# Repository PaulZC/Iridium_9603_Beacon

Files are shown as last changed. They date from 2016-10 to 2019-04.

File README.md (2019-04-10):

# Iridium 9603N Beacon

A lightweight Iridium 9603N + GNSS Beacon (Tracker)

Suitable for high altitude ballooning, asset tracking and many other remote monitoring applications.

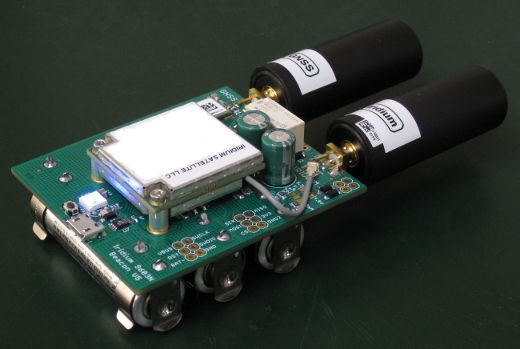
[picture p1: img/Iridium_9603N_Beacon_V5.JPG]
Iridium_9603N_Beacon_V5


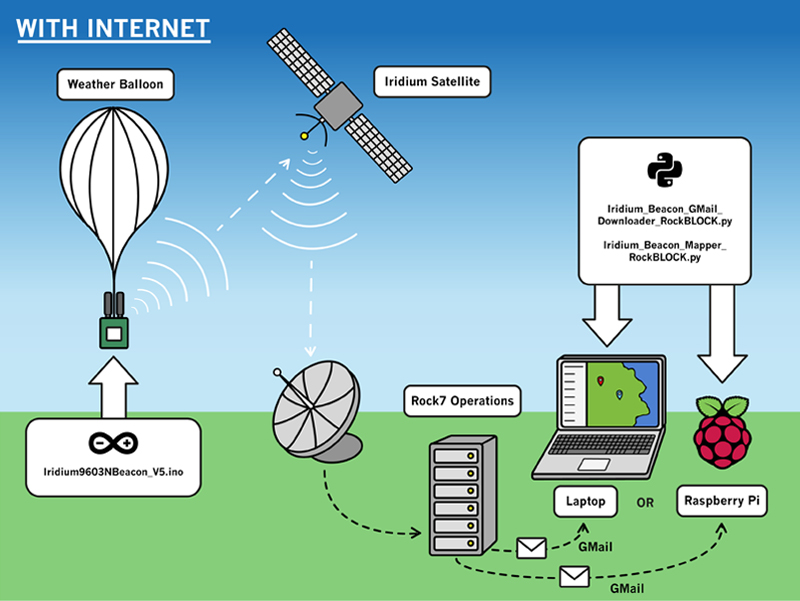
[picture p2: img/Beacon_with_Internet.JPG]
Beacon with Internet


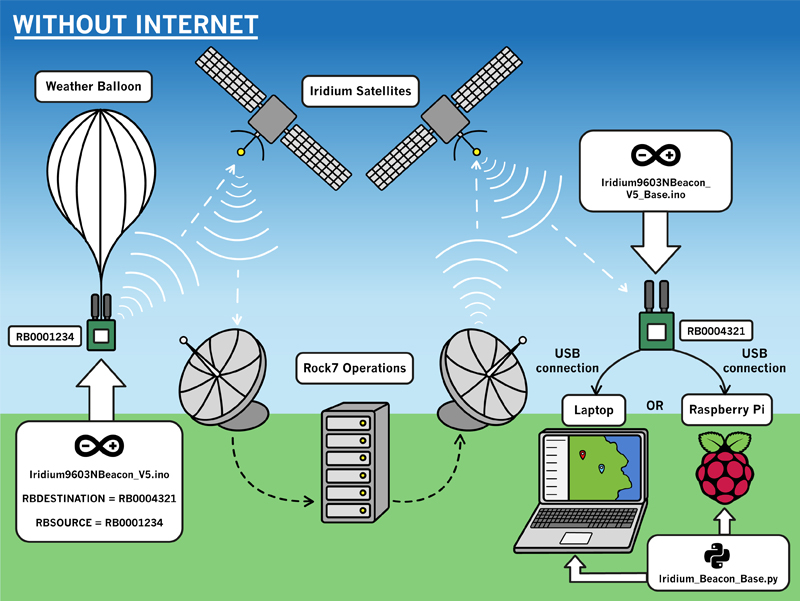
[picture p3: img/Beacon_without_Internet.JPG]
Beacon without Internet


**See [LEARN.md](https://github.com/PaulZC/Iridium_9603_Beacon/blob/master/LEARN.md) for more details.**

**See [ASSEMBLY.md](https://github.com/PaulZC/Iridium_9603_Beacon/blob/master/ASSEMBLY.md) for details on how to assemble the PCB.**

**See [RockBLOCK.md](https://github.com/PaulZC/Iridium_9603_Beacon/blob/master/RockBLOCK.md) for details on how to track your beacon from _anywhere_ using Rock7 RockBLOCK Gateway messaging.**

See [Iridium_9603_Beacon_V5.pdf](https://github.com/PaulZC/Iridium_9603_Beacon/blob/master/Iridium_9603_Beacon_V5.pdf) for the schematic, layout and Bill Of Materials.

See [Iridium_9603_Beacon_V5_BOM.xls](https://github.com/PaulZC/Iridium_9603_Beacon/blob/master/Iridium_9603_Beacon_V5_BOM.xls) for the Bill Of Materials in Excel format.

The [Eagle](https://github.com/PaulZC/Iridium_9603_Beacon/tree/master/Eagle) directory contains the schematic and pcb design files.

The [Gerber](https://github.com/PaulZC/Iridium_9603_Beacon/tree/master/Gerber) directory contains the Gerber files for the PCB. These files have been checked and used to manufacture a batch of circuit boards.

The [Arduino](https://github.com/PaulZC/Iridium_9603_Beacon/tree/master/Arduino) directory contains the Arduino code.

The [OpenSCAD](https://github.com/PaulZC/Iridium_9603_Beacon/tree/master/OpenSCAD) directory contains the .stl and .scad files for the 3D-printed covers.

The [Python](https://github.com/PaulZC/Iridium_9603_Beacon/tree/master/Python) directory contains tracking/mapping software based on the Google Static Maps API.

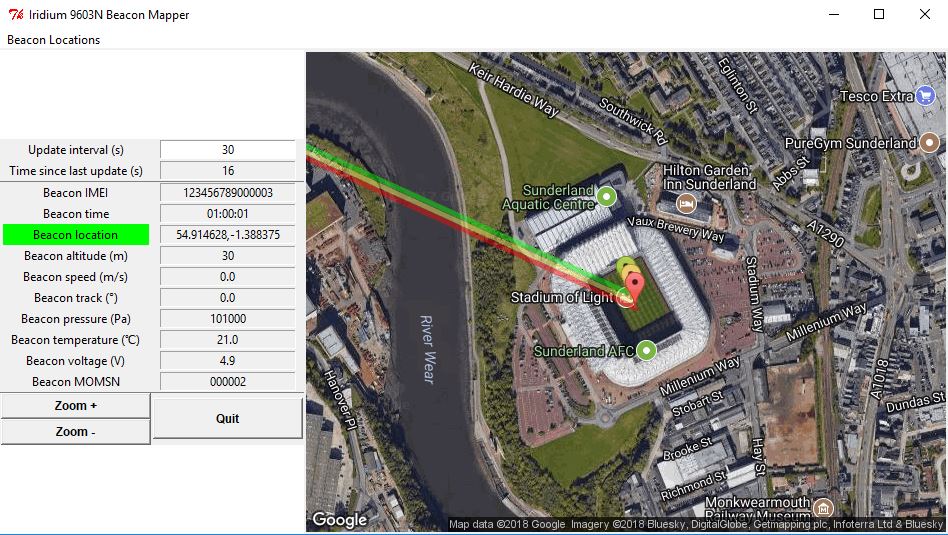
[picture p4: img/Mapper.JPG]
Mapper


See [Iridium Beacon Radio Board](https://github.com/PaulZC/Iridium_Beacon_Radio_Board) for details of the optional radio board.

Vector graphics by [Alice Clark](https://www.alicelclark.co.uk/about)

If you have found this project useful and if you are able to, please cite the paper:

P. Clark et al, An open source toolkit for the tracking, termination and recovery of high altitude balloon flights and payloads, 2019 JINST 14 P04003
[DOI:10.1088/1748-0221/14/04/P04003](https://doi.org/10.1088/1748-0221/14/04/P04003)

The Accepted Manuscript is available on arXiv: http://arxiv.org/abs/1904.04321

This project is distributed under a Creative Commons Attribution + Share-alike (BY-SA) licence.
Please refer to section 5 of the licence for the "Disclaimer of Warranties and Limitation of Liability".

Enjoy!

**_Paul_**

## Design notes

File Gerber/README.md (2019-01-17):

## Iridium 9603N Beacon - V5 Gerber Files

This directory contains the Gerber files for the V5 PCB.

Please make sure that the milling file is included during manufacture - this is required to produce the plated-through slits for the USB connector.

This project is distributed under a Creative Commons Attribution + Share-alike (BY-SA) licence.
Please refer to section 5 of the licence for the “Disclaimer of Warranties and Limitation of Liability”.

Enjoy!

**_Paul_**

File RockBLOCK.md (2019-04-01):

# Tracking Your Beacon via the RockBLOCK Gateway

The Iridium 9603N Beacon can be used to track high altitude balloons and other mobile assets. To the best of my knowledge, it hasn't yet been used
to track an elephant. But who knows! Time will tell...

I have used Iridium 9603N modules provided by other suppliers, but I recommend [Rock7](https://www.rock7.com/shop-product-detail?productId=50) since:
- They provide excellent customer support and rapid answers to technical queries
- Their web portal is really easy to use
- You can top up message credits and the monthly line rental for your modules by credit card (you don't need to set up a monthly 'standing order' payment)
- They won't charge you line rental for months where you don't make use of your 9603N module
- They provide message forwarding via their RockBLOCK Gateway which you can use to track your beacon(s) from _anywhere_ using another beacon as a 'base'

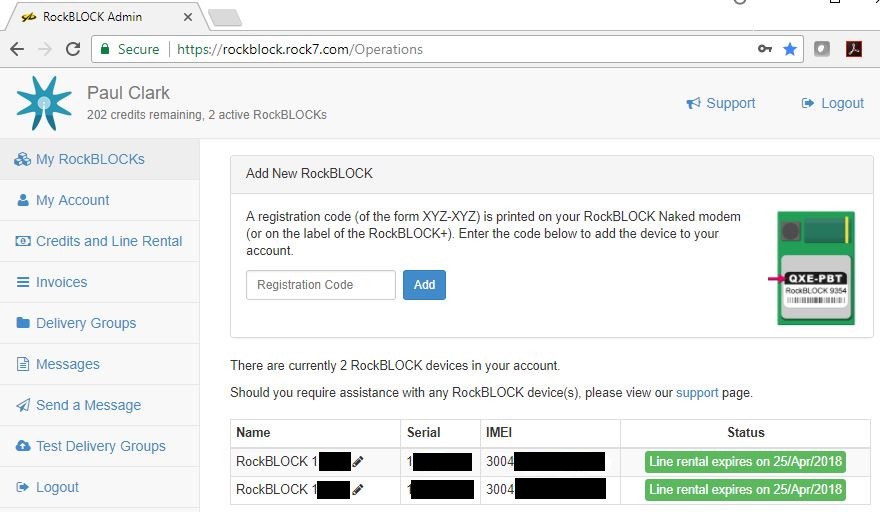
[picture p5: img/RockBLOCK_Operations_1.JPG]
RockBLOCK_Operations_1


Rock7 also provide the excellent [RockBLOCK](http://www.rock7mobile.com/products-rockblock-9603),
[RockSTAR](http://www.rock7mobile.com/products-rockstar), [RockFLEET](http://www.rock7mobile.com/products-rockfleet)
and are responsible for [YB (Yellow Brick)](https://www.ybtracking.com/products-yb3).

The beacon will send Short Burst Data messages containing its location, speed, heading, altitude, pressure and other data every five minutes by default.
Each message is automatically forwarded to whatever email address(es) you add to RockBLOCK Operations. You can simply read the email message contents and copy
and paste the position (latitude and longitude) into (e.g.) Google Maps to show where your beacon is located:

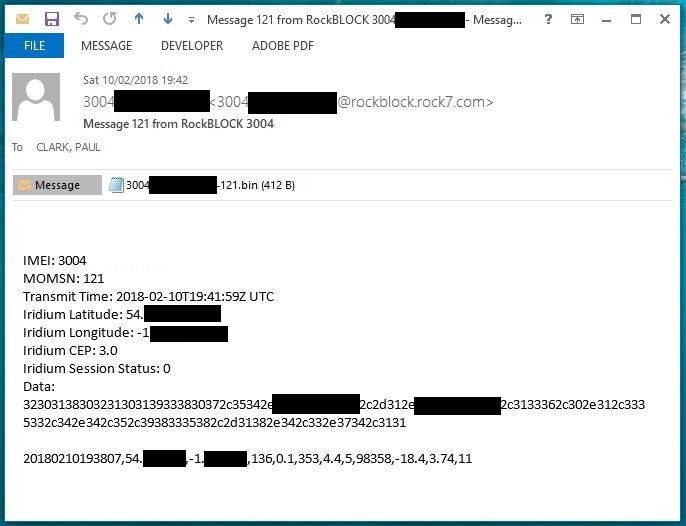
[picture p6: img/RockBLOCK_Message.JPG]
RockBLOCK_Message


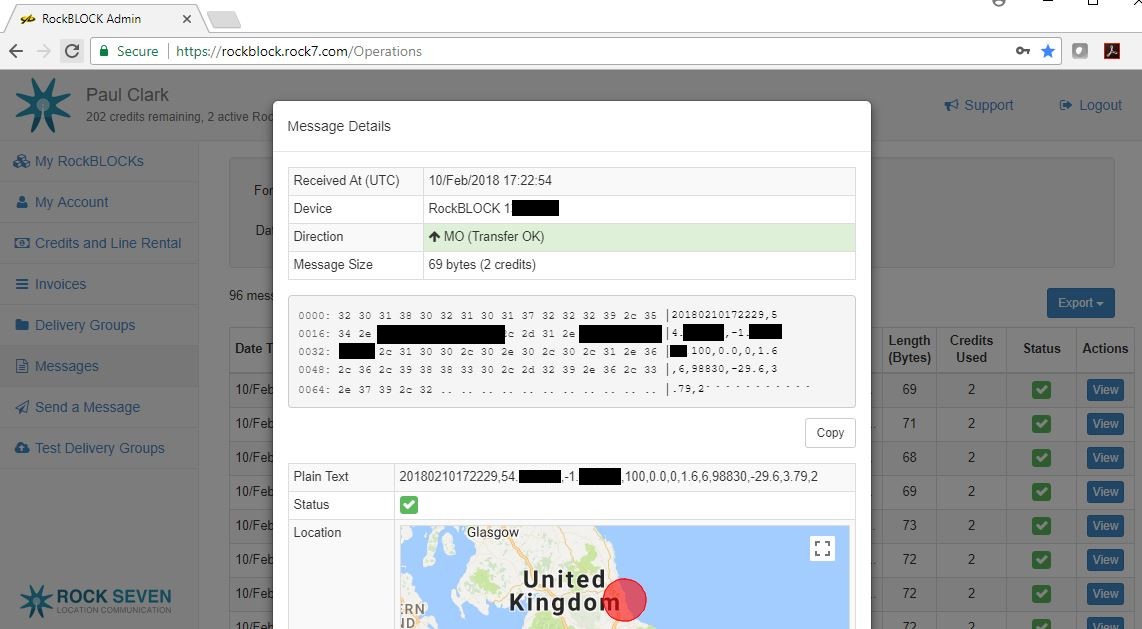
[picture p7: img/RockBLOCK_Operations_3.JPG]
RockBLOCK_Operations_3


If you have an internet connection and you want to use these emails to display the location and route of your beacon(s) on a map, you can do this using the
Iridium_Beacon_GMail_Downloader_RockBLOCK.py and Iridium_Beacon_Mapper_RockBLOCK.py mapping software
[described below](https://github.com/PaulZC/Iridium_9603_Beacon/blob/master/RockBLOCK.md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).

Beacon with Internet

If you want to be able to track your beacon(s) from somewhere _without_ an internet connection, you can use another beacon as a base, use the RockBLOCK Gateway
to automatically forward messages from your mobile beacon(s) to the base, and then display the location and route of your beacon(s) on a map using the
Iridium_Beacon_Base.py mapping software
[described below](https://github.com/PaulZC/Iridium_9603_Beacon/blob/master/RockBLOCK.md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). Map tiles for your
destination can be downloaded before your travel.

Beacon without Internet

Vector graphics by [Alice Clark](https://www.alicelclark.co.uk/about)

Message delivery via an HTTP post is possible too but, as I find email easier to work with, I won't discuss HTTP options further here.

## Configuring your Beacon via RockBLOCK Operations

The beacon uses flash memory inside the ATSAMD21G18 processor to store several settings. As flash memory is non-volatile, the settings are not forgotten if
the beacon loses power or is reset. The settings are:
- INTERVAL: the (minimum) interval between message transmissions. By default, this is set to 5 minutes
- RBDESTINATION: the serial number of the destination RockBLOCK for messages forwarded via the RockBLOCK Gateway. By default, this is set to zero which disables message forwarding
- RBSOURCE: the RockBLOCK serial number of the 9603N module on the beacon. By default, this is set to 1234 as it is not required unless you want to use message forwarding to an Iridium Becon Base

If you want to change the beacon transmission interval during a flight, you can do this through RockBLOCK Operations using the _Send a Message_
function. Select the RockBLOCK serial numbers of the beacon(s) you want to update and send a plain text message using the format _[INTERVAL=nnn]_ where _nnn_
is the new message interval in _minutes_. The interval will be updated the next time the beacon wakes up for a transmit cycle.

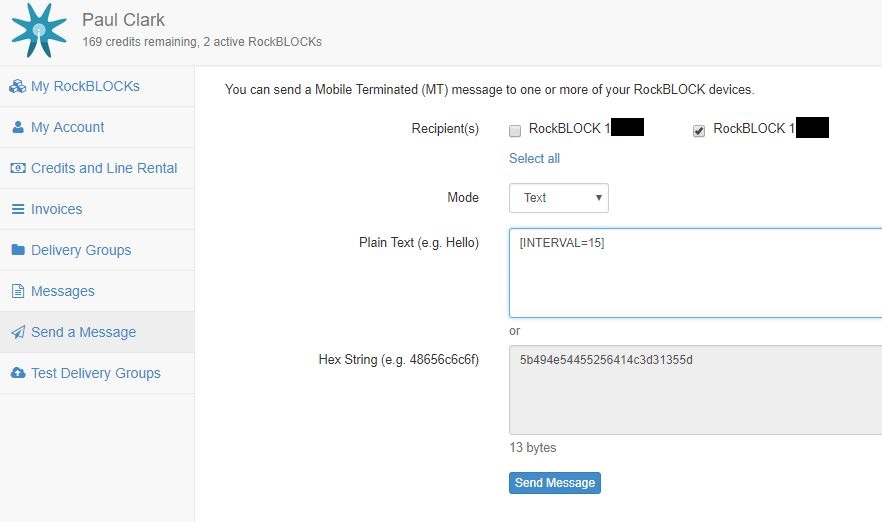
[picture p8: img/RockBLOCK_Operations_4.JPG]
RockBLOCK_Operations_4


If you want to enable message forwarding via the RockBLOCK Gateway, you can do this by including the text _[RBDESTINATION=nnnnn]_ in the RockBLOCK message where _nnnnn_
is the serial number of the destination 'base' RockBLOCK. You can disable message forwarding again by sending a message containing _[RBDESTINATION=0]_. You can change the source
serial number which is included in the messages by including the text _[RBSOURCE=nnnnn]_ in the RockBLOCK message where _nnnnn_ is the serial number of the
RockBLOCK 9603N on the beacon.

The _Send a Message_ function can also be used to control the beacon. The commands are:
- RELAY: this controls the OMRON relay on the beacon. The relay can be switched ON or OFF, or pulsed on for 1-5 seconds
- RADIO: this allows you to send a radio message from the beacon using the optional [Iridium Beacon Radio Board](https://github.com/PaulZC/Iridium_Beacon_Radio_Board)

If you want to change the state of the OMRON relay during a flight, you can do this by including the text _[RELAY=ON]_ or _[RELAY=OFF]_ in the RockBLOCK message.
The state of the relay will be updated after the next transmit cycle. If you want to pulse the relay on for 1-5 seconds, to trigger e.g. a cut-down device,
include the text _[RELAY=1]_ to pulse the relay on for 1 second then off again. _[RELAY=5]_ will pulse the relay on for five seconds then off again.
Only integer pulse durations of 1-5 seconds are valid, other values will be ignored.

If you want to send a message via the radio board, you can do this by including the text _[RADIO=nnnnnnnn]_ in the RockBLOCK message where _nnnnnnnn_ is the
message you want the eRIC radio module to transmit (e.g. the serial number of a radio-enabled cut-down device, causing it to activate). The radio board is
optional, the beacon code will work as normal without it.

The beacon can also be configured and controlled via [messages from an Iridium Beacon Base](https://github.com/PaulZC/Iridium_9603_Beacon/blob/master/RockBLOCK.md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). 

## Tracking your beacon with an internet connection

Beacon with Internet

Mapper

If you will be tracking your Iridium Beacon from somewhere with a good internet connection, then you can use:

[Iridium_Beacon_GMail_Downloader_RockBLOCK.py](https://github.com/PaulZC/Iridium_9603_Beacon/blob/master/Python/Iridium_Beacon_GMail_Downloader_RockBLOCK.py)
to check for new SBD messages and download them from a Google GMail account using the Google Mail API.

Create yourself a GMail address, follow [these instructions](https://developers.google.com/gmail/api/quickstart/python) to create your credentials and enable access for Python,
add the email address to [RockBLOCK Operations](https://rockblock.rock7.com/Operations), then when you run the code it will automatically check for the arrival of any new messages
and, when it finds one, will download the SBD .bin attachment to to your computer, mark the message as seen (read) and 'move' it to a folder called SBD by changing the message labels.
You will need to manually create the SBD folder in GMail before running the code.

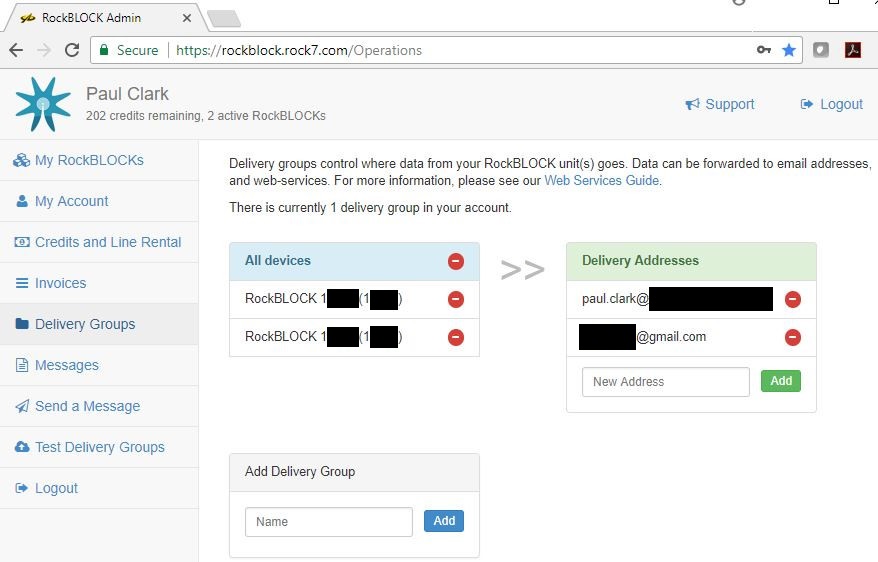
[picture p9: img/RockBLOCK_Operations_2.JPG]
RockBLOCK_Operations_2


[Iridium_Beacon_Mapper_RockBLOCK.py](https://github.com/PaulZC/Iridium_9603_Beacon/blob/master/Python/Iridium_Beacon_Mapper_RockBLOCK.py) uses the
Google Static Maps API to display the locations and paths of up to eight beacons. It will check once per minute for the appearance of new .bin
files, parse them and display the data in a Python Tkinter GUI.

You will need to download the [blank map image](https://github.com/PaulZC/Iridium_9603_Beacon/blob/master/Python/map_image_blank.png) too. This is displayed until a .bin file is processed
or whenever the GUI isn't able to download map images from the API.

You can find more details about the Google Static Maps API [here](https://developers.google.com/maps/documentation/static-maps/intro). To use the API, you will need to create
your own API Key, which you can do by following the instructions [here](https://developers.google.com/maps/documentation/static-maps/get-api-key). Copy the Key and save it in a file
called _Google_Static_Maps_API_Key.txt_ so the mapper can read it. You will need to register payment details with Google before they will issue you with a Key,
but the Standard Plan allows you to download 25,000 map images per day for free before you start being charged.

The intention is that you have Iridium_Beacon_Mapper_RockBLOCK.py and Iridium_Beacon_GMail_Downloader_RockBLOCK.py running simultaneously.
Start Iridium_Beacon_Mapper_RockBLOCK.py first and allow it to build up a dictionary of any existing .bin files, then start Iridium_Beacon_GMail_Downloader_RockBLOCK.py.
When any new SBD messages arrive in your GMail inbox, the attachments will be downloaded and then added to the map automatically.

The displayed map is automatically centered on the position of a new beacon. The center position can be changed by left-clicking in the image.
A right-click will copy that location (lat,lon) to the clipboard. The zoom level defaults to '15' but can be changed using the zoom buttons.

A pull-down menu lists the latest locations of all beacons being tracked. Click on the entry for a beacon to center the map on its location and copy its location to the clipboard.

The beacon's path is displayed as a coloured line on the map. The oldest waypoints may not be shown as the map URL is limited to 8192 characters.

The GUI uses 640x480 pixel map images. Higher resolution images are available if you have a premium plan with Google.

The GUI has been tested with Python 2.7 on 64-bit Windows and on Linux on Raspberry Pi. You will need to install the Python libraries listed below.

## Tracking your beacon _without_ an internet connection

Beacon without Internet

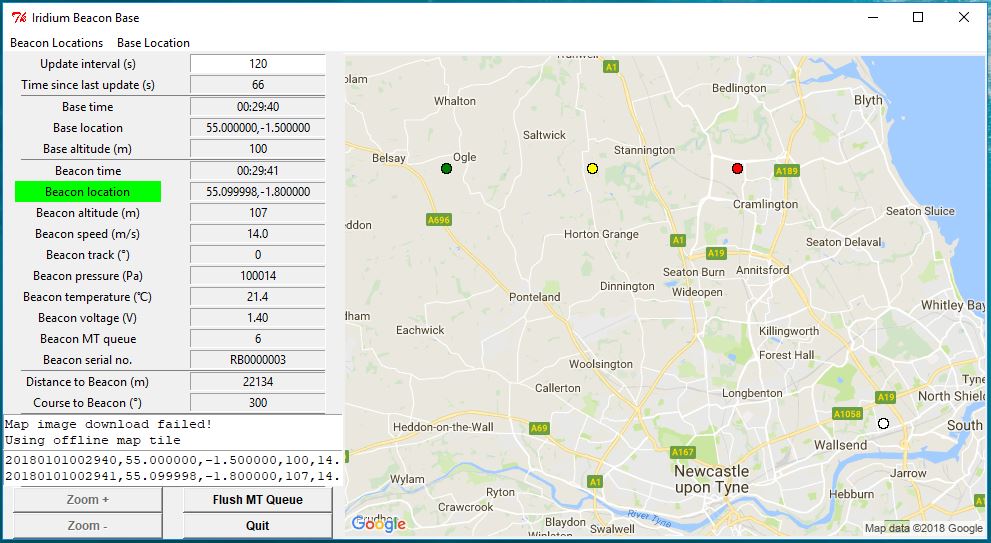
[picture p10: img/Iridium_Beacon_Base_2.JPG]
Iridium_Beacon_Base_2


Another reason I really like Rock7 is that if you prefix your SBD message with the serial number of another 'RockBLOCK', they will automatically forward
your message to that module. This means the messages from your mobile Iridium Beacon can be automatically forwarded to another Iridium Beacon acting as a 'base'
allowing you to track the beacon from _anywhere_. See the last two pages of the
[RockBLOCK-9603-Developers-Guide](http://www.rock7mobile.com/downloads/RockBLOCK-9603-Developers-Guide.pdf) for further information.

In the [Arduino](https://github.com/PaulZC/Iridium_9603_Beacon/tree/master/Arduino) directory, you will find Arduino code for both the mobile
[Iridium9603NBeacon_V5](https://github.com/PaulZC/Iridium_9603_Beacon/tree/master/Arduino/Iridium9603NBeacon_V5) and the base
[Iridium9603NBeacon_V5_Base](https://github.com/PaulZC/Iridium_9603_Beacon/tree/master/Arduino/Iridium9603NBeacon_V5_Base).

Connect the Iridium Beacon Base directly to your computer using a USB cable (as if you were going to configure it using the Arduino IDE). The Beacon Base does not need batteries,
it will draw all of its power from the USB port. The Base Python software has been tested on both a Windows laptop and Raspberry Pi.

To enable message forwarding from beacon to base, you can:
- [Send a message to the beacon from RockBLOCK Operations](https://github.com/PaulZC/Iridium_9603_Beacon/blob/master/RockBLOCK.md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)
- [Send a message to the beacon from an Iridium Beacon Base](https://github.com/PaulZC/Iridium_9603_Beacon/blob/master/RockBLOCK.md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)
- Edit the Arduino code before you download it onto the beacon

To enable message forwarding in the Arduino code: edit Iridium9603NBeacon_V5.ino, and change the line which says **#define RB_destination 0** . Change the zero to the the serial
number of the destination RockBLOCK which is acting as the base. Also change the line which says **#define RB_source 1234** . Replace the 1234 with the serial
number of the RockBLOCK 9603N you are sending the messages from.

_You will be charged twice for each message: once to send it from the Beacon (Mobile Originated); and a second time to receive it on the base (Mobile Terminated)._

Before you travel, download a set of Google Static Map tiles using
[Google_Static_Maps_Tiler.py](https://github.com/PaulZC/Iridium_9603_Beacon/blob/master/Python/Google_Static_Maps_Tiler.py). 1 degree tiles are useful for
large areas, 0.1 degree or 0.01 degree for smaller areas. Put all the _StaticMapTile----.png_ files in the same directory as Iridium_Beacon_Base.py. By default, the
Tiler will ask Google for _roadmap_ map_type images. You can change this to _satellite_, _terrain_ or _hybrid_ by editing the Python code before you run it.

[Iridium_Beacon_Base.py](https://github.com/PaulZC/Iridium_9603_Beacon/blob/master/Python/Iridium_Beacon_Base.py) is very similar in its operation to
Iridium_Beacon_Mapper_RockBLOCK.py except that the beacon data is received via Iridium rather than by email. The software talks to
Iridium9603NBeacon_V5_Base via Serial (over USB) and displays the beacon and base locations using the
[Google Static Maps API](https://developers.google.com/maps/documentation/static-maps/intro).

To use the Google Maps API, you will need to create your own API Key, which you can do by following the instructions [here](https://developers.google.com/maps/documentation/static-maps/get-api-key).
Copy the Key and save it in a file called _Google_Static_Maps_API_Key.txt_ so the mapper can read it. You will need to register payment details with Google before they will issue you with a Key,
but the Standard Plan allows you to download 25,000 map images per day for free before you start being charged.

Before running the Iridium_Beacon_Base.py code, plug the Iridium Beacon Base into your computer and find out its serial port number:
- Under Windows, you can run Device Manager from the Control Panel or using the search tool (magnifying glass). Open the entry for _Ports (COM & LPT)_. The base will be listed as a COM port
- Under Linux (e.g. on Raspberry Pi), you can find the port number by typing _ls /dev_ in a terminal window. The base will usually appear as _/ttyACM0_

Every 'update' seconds the GUI talks to the base beacon and:
- requests its GNSS data including time, position and altitude;
- starts an IridiumSBD session and downloads a packet from the mobile terminated queue (if any are present).

The GUI and base provide access to the RockBLOCK FLUSH_MT function, so an excess of unread Mobile Terminated messages from your beacon(s) can be discarded if required
(note that you are still charged from these messages!).

The software logs all received packets to CSV log files. Each beacon gets its own log file.

The software makes extensive use of the Google Static Map API:
- The displayed map is automatically centered on a new beacon position.
- The center position can be changed by left-clicking in the image.
- A right-click will copy the click location (lat,lon) to the clipboard.
- The zoom level is set automatically when a new beacon is displayed to show both beacon and base.
- The zoom can be changed using the buttons.

When you are online, the path of each beacon is displayed as a coloured line on the map. The oldest waypoints may be deleted as the map URL is limited to 8192 characters.

A pull-down menu lists the locations of all the beacons being tracked. Clicking on a menu entry will center the map on that location and will copy
the location to the clipboard.

A second pull-down menu shows the location of the base. Clicking it will center the map on that location and will copy that location to the clipboard.

A third pull-down menu lets you send a configuration update message to a beacon. See
[Configuring your Beacon via Iridium Beacon Base](https://github.com/PaulZC/Iridium_9603_Beacon/blob/master/RockBLOCK.md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)
for further details.

A fourth pull-down menu lets you set the update interval of the base software. You are charged each time you check for new messages, so make sure you set
update to a sensible value. If your beacon is transmitting messages every 10 minutes, then set the update interval to 10 minutes too. If there is a backlog
of messages you want to download, then reduce update accordingly. But remember to set it back to 10 minutes afterwards to avoid being charged unnecessarily.
If you are tracking two beacons each sending messages every 10 minutes, then set update to 5 minutes.

The GUI uses 640x480 pixel map images. Higher resolution images are available if you have a premium plan with Google.

When you are online, the user interface will look like this:

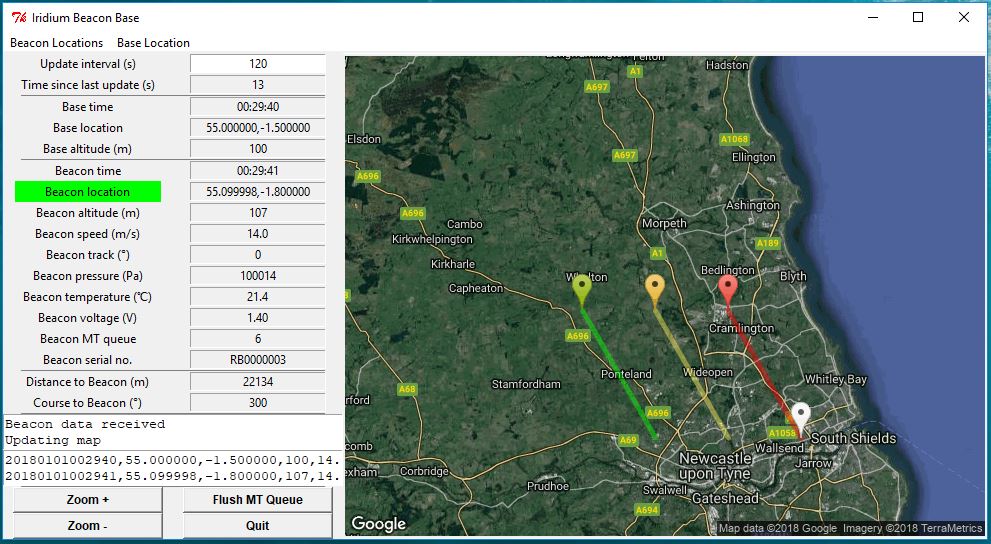
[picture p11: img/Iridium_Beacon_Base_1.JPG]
Iridium_Beacon_Base_1


When you are offline, the software will use the map tiles from the Tiler. Base and beacon locations will be shown on the offline maps but not path information

Iridium_Beacon_Base_2

## Configuring your Beacon via Iridium Beacon Base

[Iridium_Beacon_Base.py](https://github.com/PaulZC/Iridium_9603_Beacon/blob/master/Python/Iridium_Beacon_Base.py) has a pull-down menu which allows you to send
a message to one of your beacons so you can control or configure it.

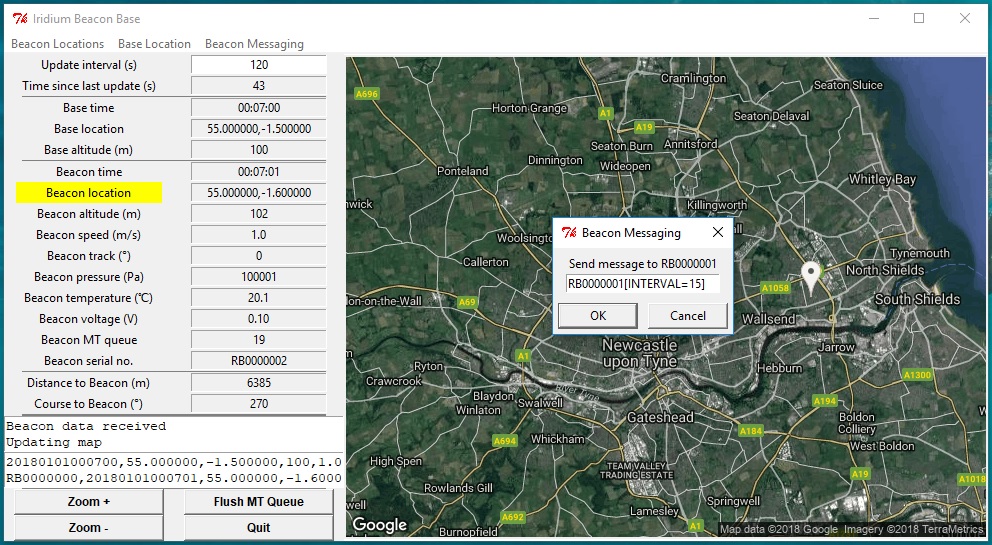
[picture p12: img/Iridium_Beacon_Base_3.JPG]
Iridium_Beacon_Base_3


By default, RBDESTINATION is set to zero in the Iridium Beacon code which disables message forwarding. To enable message forwarding, we need to change the RBDESTINATION
to the RockBLOCK serial number of the Iridium Beacon Base. Messages from the beacon will then be sent by email as usual, but also automatically forwarded via a second
Iridium message to the base so the base can track the beacon. _You are charged for both messages._

If the base software is not currently tracking any beacons, the Beacon Messaging pull-down menu will only contain a dummy entry for _RB0000000_. Click on that entry
and a dialogue box will appear containing the text _RB0000000[INTERVAL=5]_. Delete all of the text and replace it with:
- _RBxxxxx[RBDESTINATION=yyyyy][RBSOURCE=xxxxx]_

where
- _xxxxx_ is the RockBLOCK serial number of the 9603N _on the beacon_
- _yyyyy_ is the RockBLOCK serial number of the 9603N _on the base_

and then click OK.

Make sure you include the square brackets. Any commands not enclosed in square brackets are ignored.

The message will be sent from the 9603N on the base, through the Iridium network to the RockBLOCK Gateway. The RockBLOCK Gateway will then automatically forward
the message back through the Iridium network to beacon _xxxxx_. Beacon _xxxxx_ will receive the new RBDESTINATION and RBSOURCE the next time it wakes up and transmits a fix.

Now, each time beacon _xxxxx_ sends a message, it will be automatically prefixed with the serial number of the base (_RByyyyy_) and forwarded to the base through
the RockBLOCK Gateway.

Once the base software has received a message from beacon _xxxxx_, its serial number will appear in the Beacon Messaging pull-down menu to make it easier to send
more messages to that beacon.

If you want to disable message forwarding, send a message to beacon _xxxxx_ containing the text:
- _RBxxxxx[RBDESTINATION=0]_

If you want to change the message interval of a beacon, send it a message containing:
- _RBxxxxx[INTERVAL=nnn]_

where
- _nnn_ is the new message interval in _minutes_

Valid values are 1 to 1440 (once per minute to once per day). The beacon will download and process the message during its next transmit cycle. The new interval will take effect after the _following_ transmission.

If you want to change the status of the OMRON relay on board the beacon, add the text _[RELAY=ON]_ or _[RELAY=OFF]_ to the message. If you want to pulse the
relay on for 1-5 seconds, to trigger e.g. a cut-down device, add the text _[RELAY=1]_ to pulse the relay on for 1 second then off again. _[RELAY=5]_ will pulse
the relay on for 5 seconds then off again. Only integer pulse durations of 1-5 seconds are valid, other values will be ignored. 
The relay status will be updated at the end of the beacon's transmit cycle.

If you want the (optional) radio board to transmit a message, add the text _[RADIO=nnnnnnnn]_ to the message, where _nnnnnnnn_ is the message you want the radio
board to transmit. Usually _nnnnnnnn_ is the serial number of the eRIC radio module on a cut-down device.

## Extras

[Iridium_Beacon_Stitcher_RockBLOCK.py](https://github.com/PaulZC/Iridium_9603_Beacon/blob/master/Python/Iridium_Beacon_Stitcher_RockBLOCK.py) will stitch the .bin SBD attachments downloaded by
[Iridium_Beacon_GMail_Downloader_RockBLOCK.py](https://github.com/PaulZC/Iridium_9603_Beacon/blob/master/Python/Iridium_Beacon_GMail_Downloader_RockBLOCK.py) together into a single .csv
(Comma Separated Value) file which can be opened by (e.g.) Microsoft Excel.

[Iridium_Beacon_CSV_DateTime.py](https://github.com/PaulZC/Iridium_9603_Beacon/blob/master/Python/Iridium_Beacon_CSV_DateTime.py) will convert the first column of the stitched .csv file
from YYYYMMDDHHMMSS format into DD/MM/YY,HH:MM:SS format, making the message timing easier to interpret using Excel.

[Iridium_Beacon_DateTime_CSV_to_KML_RockBLOCK.py](https://github.com/PaulZC/Iridium_9603_Beacon/blob/master/Python/Iridium_Beacon_DateTime_CSV_to_KML_RockBLOCK.py) will convert the .csv file produced by
[Iridium_Beacon_CSV_DateTime.py](https://github.com/PaulZC/Iridium_9603_Beacon/blob/master/Python/Iridium_Beacon_CSV_DateTime.py) into .kml files which can be opened in Google Earth.
The path of the beacon can be shown as: 2D (course over ground) or 3D (course and altitude) linestring; points (labelled with message sequence numbers); and arrows (indicating the heading of the beacon).

[Iridium_Beacon_BIN_to_KML_RockBLOCK.py](https://github.com/PaulZC/Iridium_9603_Beacon/blob/master/Python/Iridium_Beacon_BIN_to_KML_RockBLOCK.py) will convert the individual .bin SBD attachments downloaded by
[Iridium_Beacon_GMail_Downloader_RockBLOCK.py](https://github.com/PaulZC/Iridium_9603_Beacon/blob/master/Python/Iridium_Beacon_GMail_Downloader_RockBLOCK.py) into .kml files which can be opened in Google Earth.
The path of the beacon can be shown as: 2D (course over ground) or 3D (course and altitude) linestring; points (labelled with message sequence numbers); and arrows (indicating the heading of the beacon).

[Iridium_Beacon_habhub_habitat_uploader_RockBLOCK.py](https://github.com/PaulZC/Iridium_9603_Beacon/blob/master/Python/Iridium_Beacon_habhub_habitat_uploader_RockBLOCK.py) will parse the data in the .bin SBD attachments
downloaded by [Iridium_Beacon_GMail_Downloader_RockBLOCK.py](https://github.com/PaulZC/Iridium_9603_Beacon/blob/master/Python/Iridium_Beacon_GMail_Downloader_RockBLOCK.py) and upload the data to the excellent
[HabHub Habitat Tracker](https://tracker.habhub.org). Start the uploader first and allow it to build up a list of any existing SBD .bin files, then start the GMail_Downloader.
When any new SBD messages arrive in your GMail inbox, they will be downloaded and then uploaded to habitat automatically. You will find the lines that actually upload the data to Habitat are commented out.
Only uncomment them once you have registered your flight with UKHAS and are ready to upload real data.

## Required Python 2.7 Libraries

To get the tools to run successfully you will need to install the following libraries:

### GMail API and oauth2client

- pip install --upgrade google-api-python-client oauth2client

### PIL ImageTk

- sudo apt-get install python-pil.imagetk

### Matplotlib

- sudo apt-get install python-matplotlib

### Kyle Lancaster's simplekml

- http://simplekml.readthedocs.io/en/latest/index.html
- https://pypi.python.org/pypi/simplekml
- pip install simplekml

### CouchDB

- pip install couchdb

or

- Go to https://pypi.org/project/CouchDB/#files
- Download the source tar.gz
- Extract it and cd into the folder
- sudo python setup.py install

### CRCMOD

- pip install crcmod

or

- Go to https://pypi.org/project/crcmod/#files
- Download the source tar.gz
- Extract it and cd into the folder
- sudo python setup.py install

###

Enjoy!

**_Paul_**

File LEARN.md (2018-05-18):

# Iridium 9603N Beacon

A lightweight Iridium 9603N + GNSS Beacon (Tracker)

Suitable for high altitude ballooning, asset tracking and many other remote monitoring applications.

New hardware features for Version 5:
- Includes an OMRON G6SK relay to allow the beacon to control external equipment (e.g. a cut-down device)
- 9603N EXT_PWR is now switched via a P-MOSFET

New software features for Version 5:
- Relay can be configured during a flight via a Mobile Terminated SBD message

Iridium_9603N_Beacon_V5

## Background

In response to feedback received from balloon enthusiasts, version 5 of the Iridium 9603N Beacon provides:
an OMRON G6SK bistable relay to allow the beacon to control external equipment (e.g. a cut-down device);
Iridium 9603n EXT_PWR power switching via a P-MOSFET.

Version 5 is slightly heavier than version 3. So, if you are looking for a very lightweight (60g) solar tracker for your long-duration high alitude balloon
flight, you might be better off with [version 3](https://github.com/PaulZC/Iridium_9603_Beacon/blob/master/Archive/V3/README.md). If you want a more robust
tracker for shorter-duration, battery-powered flights where the tracker stands a better chance of continuing to transmit while on the ground,
then version 5 is probably for you.

## The Design

See [Iridium_9603_Beacon_V5.pdf](https://github.com/PaulZC/Iridium_9603_Beacon/blob/master/Iridium_9603_Beacon_V5.pdf) for the schematic,
layout and Bill Of Materials.

See [Iridium_9603_Beacon_V5_BOM.xls](https://github.com/PaulZC/Iridium_9603_Beacon/blob/master/Iridium_9603_Beacon_V5_BOM.xls) for the Bill Of Materials in Excel format.

The [Eagle](https://github.com/PaulZC/Iridium_9603_Beacon/tree/master/Eagle) directory contains the schematic and pcb design files.

Here's how the completed PCB looks when configured for USB or battery power (using 1F super capacitors):

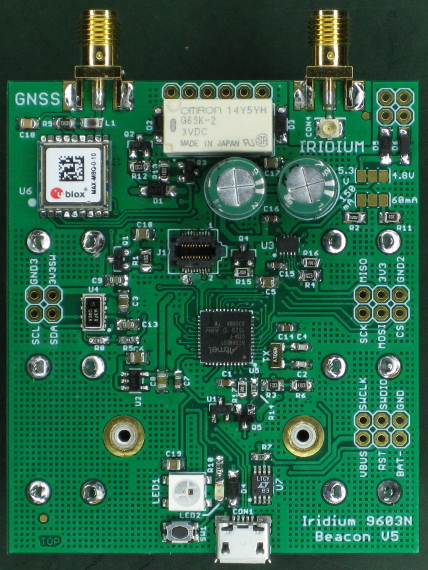
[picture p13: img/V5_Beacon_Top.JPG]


And here's how it looks from underneath when configured for battery power:

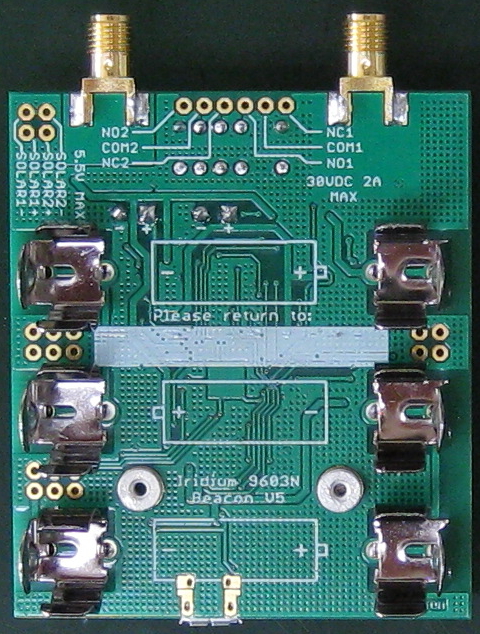
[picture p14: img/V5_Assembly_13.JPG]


The key components of V5 of the Iridium 9603N Beacon are:

### Iridium 9603N Module
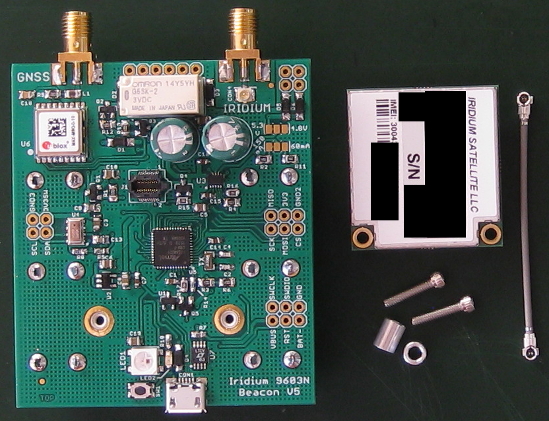
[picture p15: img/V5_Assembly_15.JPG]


Available from:
- https://www.rock7.com/shop-product-detail?productId=50

Other UK and International distributors can be found at:
- https://www.iridium.com/where-to-buy/?pid=27083

Make sure you purchase the 9603N and not the older 9603. The 9603N will run from 5V ± 0.5V which is important as the super capacitor charger is set to produce 5.3V; the older 9603 is only rated to 5V ± 0.2V.
If you do have the older 9603, you can change the super capacitor voltage to 4.8V by reconfiguring the split pads next to the super capacitors.

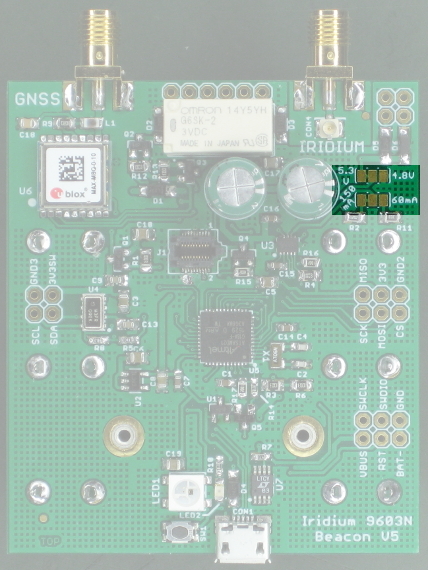
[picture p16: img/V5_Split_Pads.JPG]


### SMA Iridium Antenna
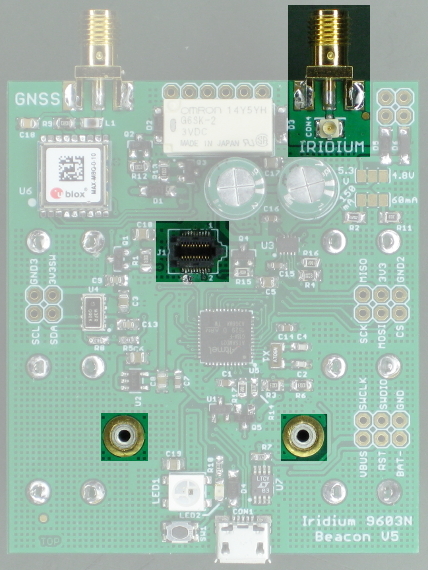
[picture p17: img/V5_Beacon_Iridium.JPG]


An Iridium SMA helical antenna (e.g. the Maxtena M1621HCT-SMA, available from Farnell / Element 14 (2281619)) can be connected to the 9603N with a short Molex uFL cable (part number 73412-0508, available from Farnell / Element14 (1340201))

### Atmel ATSAMD21G18 Processor
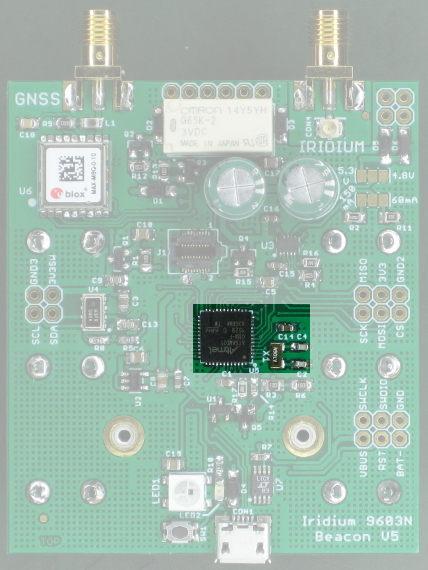
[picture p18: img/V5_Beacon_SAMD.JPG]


As used on the Adafruit Feather M0:
- https://www.adafruit.com/products/2772

Available from e.g. Farnell / Element14 (2460544)

### MPL3115A2 Altitude/Pressure sensor:
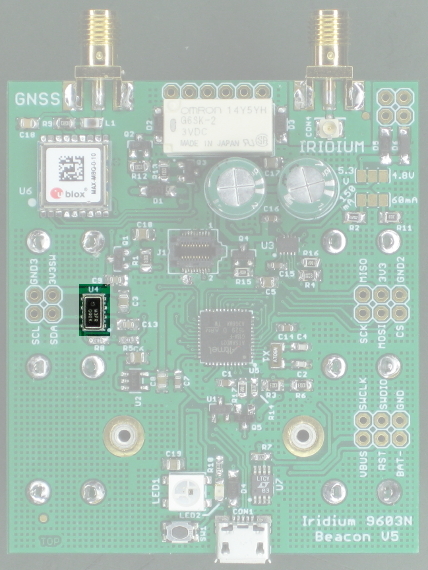
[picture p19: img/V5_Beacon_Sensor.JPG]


As used on the Sparkfun SEN-11084
- https://www.sparkfun.com/products/11084

Available as a bare chip from e.g. Farnell / Element14 (2009084)

### Linear Technology LTC3225EDDB SuperCapacitor Charger
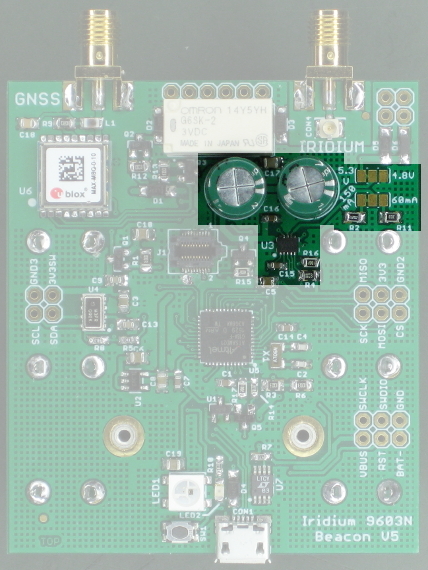
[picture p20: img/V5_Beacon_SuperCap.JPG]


- http://www.linear.com/product/LTC3225

Available as a bare chip from e.g. Farnell / Element14 (1715231)

### u-blox MAX-M8Q GNSS
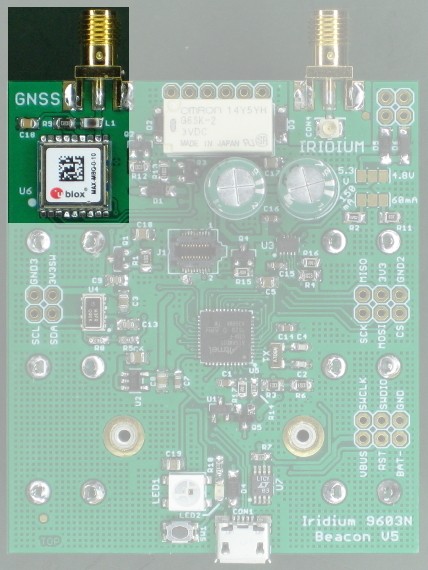
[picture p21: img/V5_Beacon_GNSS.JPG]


- https://www.u-blox.com/en/product/max-m8-series

Connect an antenna (e.g. the Maxtena M1516HCT-P-SMA, available from Farnell / Element 14 (2484960)) using the SMA connector. 3V power for an active antenna is provided.

### MCP111T-240 Reset Supervisor
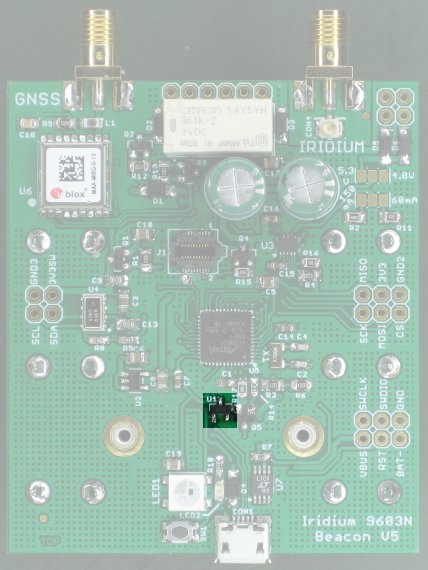
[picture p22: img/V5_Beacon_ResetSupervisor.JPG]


The SAMD21G18 has a built-in power-on reset and brown-out detector circuit, but it doesn't work properly if the supply voltage rises very slowly.
The SAMD21G18 datasheet isn’t much help here. Section 8.2.4.1 specifies:
- _Minimum Rise Rate_

   _The integrated power-on reset (POR) circuitry monitoring the VDDANA power supply requires a minimum rise rate._

But then the supply characteristics section (37.4) specifies a _maximum_ supply rise rate of 0.1V/µs, not a minimum.

Tests I've carried out show that the processor will reset correctly if the power supply ramps up at 0.3 V/s or more, but fails to reset correctly at 0.2 V/s or less.
As the solar panel voltage will ramp up very slowly at sunrise, I've included a separate reset supervisor.
The Microchip MCP111-240 has an open drain output which holds the processor in reset until the supply rises above 2.4V, ensuring a clean start.

### SPX3819-3.3 Voltage Regulator
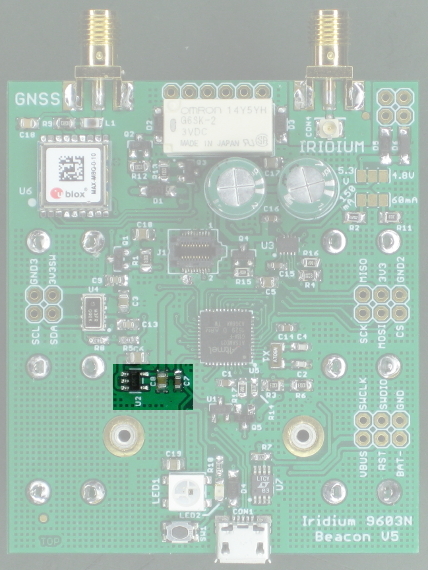
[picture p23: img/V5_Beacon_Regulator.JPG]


The SPX3819-3.3 Voltage Regulator regulates the output from the two solar panels, or the batteries, or the USB port, providing 3.3V for the processor, GNSS and pressure sensor.

The LTC3225EDDB SuperCapacitor Charger draws its power directly from the solar panels, batteries or USB without going through the regulator.

MBR120 diodes protect the solar panels, USB port and the batteries from each other.

### WS2812B "NeoPixel"
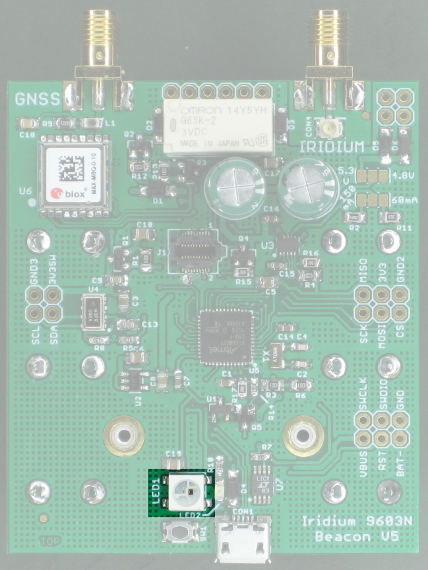
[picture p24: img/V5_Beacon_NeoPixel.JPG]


A tri-colour NeoPixel has been included on Version 4 to show the status of the beacon:
- Magenta at power up (loop_step == init) (~10 seconds)
- Blue when waiting for a GNSS fix (loop_step == start_GPS or read_GPS or read_pressure) (could take 5 mins)
- Cyan when waiting for supercapacitors to charge (loop_step == start_LTC3225 or wait_LTC3225) (could take 7 mins)
- White during Iridium transmit (loop_step == start_9603) (could take 5 mins)
- Green flash (2 seconds) indicates successful transmission
- Red flash (2 seconds) entering sleep
- LED will flash Red after: Iridium transmission (successful or failure); low battery detected; no GNSS data; supercapacitors failed to charge

### LT1634BCMS8-1.25 1.25V Voltage Reference
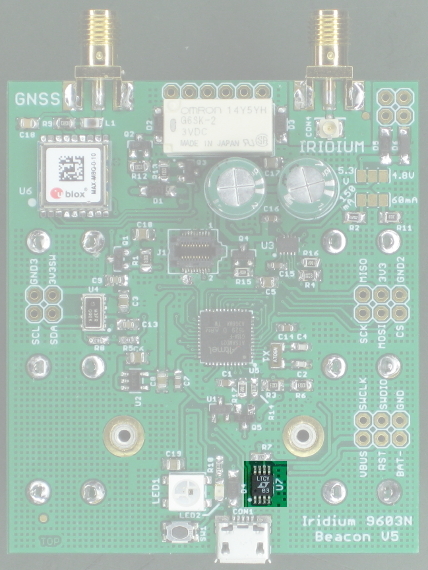
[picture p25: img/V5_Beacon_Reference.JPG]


The SAMD21G18 processor is powered from a low drop-out 3.3V regulator. The solar / USB / battery voltage is measured via an analog pin connected to the mid point
of two 100K resistors configured as a voltage divider. The voltage measured by the analog pin is relative to the regulator voltage. When the power voltage drops below approximately
3.7V, the regulator voltage starts to collapse. The analog voltage appears to never drop below approximately 3.4V even when the actual voltage is lower than this.

By adding a 1.25V voltage reference and connecting it to a second analog pin, its constant voltage will appear to increase as the regulator voltage starts to collapse.
This voltage increase can be used to correct the power voltage measurement.

## Iridum 9603N Power Switching

The datasheet for the 9603N contains a note which says:

_When a transceiver has been turned off, Product Developers should not reapply power on a unit until more than 2 seconds has elapsed after power has reached 0V. Additionally, if a unit does not respond to AT commands, power off the module, wait for 2 seconds and then power it back on._

_When a 9603 is powered off the power on reset circuit requires 2 seconds for voltages to decay. If the 2 second wait time is not adhered to the reset circuit may not operate and the modem could be placed in a non-operational state. The state is not permanent and can be rectified by the above procedure._

I have seen a 9603N go into this non-operational state only twice across the ten beacons I have in operation. Unfortunately, with the previous versions of the beacon design,
the only way to completely remove power to the 9603N was to manually discharge the super capacitors with a 10 Ohm resistor. Obviously it would be disastrous if this happened
during a flight. So, V5 of the beacon contains an additional P-MOSFET (Q4) to disconnect the power to the 9603N.

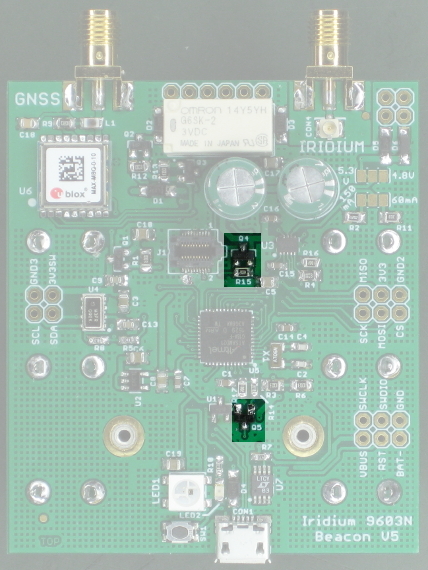
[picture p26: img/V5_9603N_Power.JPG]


## How much does the V5 beacon weigh?

Configured for battery operation, including three Energiser® Ultimate Lithium AA batteries and the Maxtena SMA antennas listed in the BOM, it weighs 112.8g.

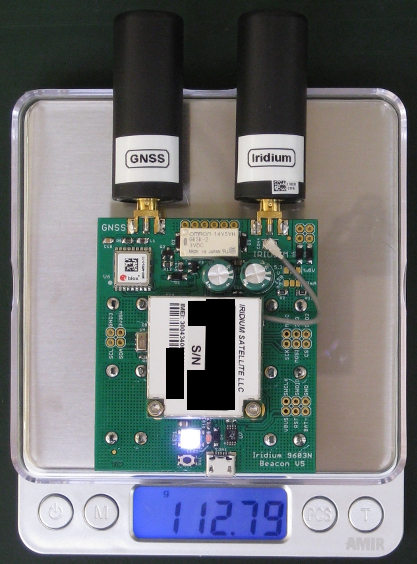
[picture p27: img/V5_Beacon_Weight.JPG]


The weight breaks down as follows:
- Batteries: 45.3g
- Populated PCB with 1F supercapacitors and battery clips: 29.7g
- Iridium module with mounting hardware and uFL cable: 13.0g
- Iridium antenna: 12.5g
- GNSS antenna: 12.3g

Running from solar power, the total weight would be approximately 76.5g:
- Populated PCB with 10F supercapacitors: 27.4g
- Iridium module with mounting hardware and uFL cable: 13.0g
- Iridium antenna: 12.5g
- GNSS antenna: 12.3g
- Solar panels (2): 6.3g
- Support hardware for the solar panels: 5g

## Power Options 
V5 of the Iridium 9603N Beacon can draw power from: the solar panels; three AA batteries; or USB.
It is possible to connect all three or any two simultaneously, the beacon will simply draw power from whichever is providing the higher voltage.

If you are going to use solar power, use 10F super capacitors and a charge current of 60mA. Install the capacitors on the underside of the PCB, carefully
bending the legs to fit. Here is how they look on version 3 of the PCB:

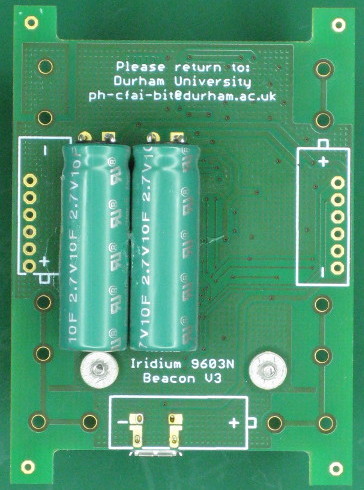
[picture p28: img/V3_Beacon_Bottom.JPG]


If you are going to run exclusively from batteries or USB, then 1F super capacitors will suffice with the default charge current of 150mA.

The charge current can be changed by reconfiguring the split pads next to the super capacitors.



(The LTC3225 draws approximately _twice_ the chosen charge current. 300mA would be way too much for the PowerFilm solar panels.)

### Two PowerFilm Solar MPT3.6-150 solar panels




- http://www.powerfilmsolar.com/products/?mpt36150&show=product&productID=271537&productCategoryIDs=6573

Available (in the UK) from e.g.:
- http://www.selectsolar.co.uk/prod/264/powerfilm-mpt36150-100ma-36v-mini-solar-panel

You will want to angle the solar panels at +/- 45 degrees with respect to the circuit board so that at least one panel will collect sunlight while the sun is low in the sky.
When the sun is overhead, both panels will collect sunlight.

### Do the batteries really work at altitude?

Yes. Version 1 of the beacon was powered by three Energiser® Ultimate Lithium AAA batteries and sent updates
[from the UK all the way to China](https://github.com/PaulZC/Iridium_9603_Beacon/blob/master/Archive/V2/Iridium_9603_Beacon.pdf).

Here are the results of a 24 hour cold test on version 4 using dry ice. Messages were sent every 15 minutes. You can see that the AA battery voltage does vary with temperature
but at close to -40C the batteries are still providing ample voltage. There was still plenty of battery capacity remaining when I terminated the test after 24 hours (to save on message costs!).



### Do I need to be careful around the battery clips?

Yes! The clips are of course conductive. If you place the beacon battery-side down on a conductive surface **BAD THINGS WILL HAPPEN!**

### Why do you need the Super Capacitors?
The Iridium 9603 module draws an average current of 145mA and a peak current of 1.3A when transmitting its short data bursts. That’s too much for the solar panels to provide.
The LTC3225 super capacitor charger draws a lower current from the panels to slowly charge two 2.7V capacitors, connected in series, to 5.3V. The capacitors then deliver the 1.3A to the module when it sends the data burst.

### Why is the Super Capacitor Charger charge current set to 60mA / 150mA?
The datasheet for the 9603N quotes: an average idle current of 34mA; and an average receive current of 39mA.

For solar operation, we need to charge the capacitors at a higher current than 39mA, but keep the total current draw within what the solar panels can deliver.
(Remember that the LTC3225 draws approximately _twice_ the chosen charge current.)
The 10F capacitors provide the majority of the higher current draw during the transmit cycle.

For USB or battery operation, setting the super capacitor charge current to 150mA results in the capacitors only being needed to provide the 1.3A peak current when the 9603N is actually transmitting a data burst.
This means smaller (1F) capacitors are adequate.

### Can I leave the USB connected during testing?
Yes. Leaving the USB connected is useful as you can monitor the Serial messages produced by the code in the Arduino IDE Serial Monitor.
If you use a standard USB cable then the beacon will draw power from USB. To test the beacon running on solar power, you will need to break the USB 5V power connection.
You can do this with a home-made power-break cable.

Take a short male to female USB extension cable; carefully strip the outer sheath from cable somewhere near the middle;
prise apart the screen connection to reveal the four USB wires (red (5V); black (GND); green and white (data)); cut and insulate the ends of the red 5V wire leaving the black, green and white wires and the screen connection intact:



### Which AA batteries should I use?
Energiser® Ultimate Lithium batteries. These are rated down to -40°C but tests I’ve done (using dry ice) show that they continue to work much colder than that.
Please see the [V2 documentation](https://github.com/PaulZC/Iridium_9603_Beacon/blob/master/Archive/V2/Iridium_9603_Beacon.pdf) for further details.

## IO Pins


**SWCLK** and **SWDIO** are used during [programming of the SAMD bootloader](https://github.com/PaulZC/Iridium_9603_Beacon/blob/master/LEARN.md#how-do-i-install-the-atsamd21g18-bootloader)

**3V3SW** is the 3.3V power rail switched by Q1 and which provides power for the MAX-M8Q GNSS and MPL3115A2 altitude sensor.
You can use this pin to provide power for a peripheral which you want to be able to disable to save power.

**SDA** and **SCL** are the I2C bus data and clock signals.
You can use these to connect another I2C sensor but be aware that it will share the bus with the MPL3115A2.

**3V3** is the 3.3V power rail from the SPX3819-3.3 voltage regulator.
Any peripherals connected to this will be continuously powered when power is available from the solar panels, batteries or USB.

**MISO**, **SCK**, **MOSI** and **SD_CS** are the SPI bus data, clock and enable connections.
You could use these to connect SD storage or another SPI peripheral.

**BAT-** is connected to the negative battery terminal. A link on the top layer of the PCB connects the BAT- pad to the adjacent GND pad.
If you want the beacon to have a true on/off switch when running on battery power: cut the link between the BAT- and GND pads;
wire a SPST switch to the two pads.

## Do you recommend coating the board once it is populated?
As a minimum, I’d recommend applying a coat of acrylic protective lacquer to the processor and surrounding components (especially the crystal).
If you’re using an aerosol, be careful to mask off the connectors, switch and the pressure sensor first.



## Arduino Code
The [Arduino](https://github.com/PaulZC/Iridium_9603_Beacon/tree/master/Arduino) directory contains the Arduino code.

The code is based extensively on Mikal Hart’s IridiumSBD Beacon example:
- https://github.com/mikalhart/IridiumSBD/tree/master/examples/Beacon

The main loop is structured around a large switch / case statement which:
- Initialises the serial ports; checks the solar panel voltage
- Powers up the GPS and MPL3115A2; checks the solar panel voltage
- Waits until the GPS establishes a fix; checks the solar panel voltage
- Reads the temperature and pressure from the MPL3115A2
- Powers down the GPS and powers up the LTC3225EDDB supercapacitor charger; checks the solar panel voltage
- Waits for the supercapacitors to charge; checks the solar panel voltage
- Queues the Iridium message transmission; checks the solar panel voltage
- Powers everything down and puts the processor to sleep until the next alarm interrupt

If the solar panel voltage falls below a useful level at any time, the code jumps to the sleep case and waits for the next alarm interrupt.

The BEACON_INTERVAL is stored in non-volatile (flash) memory internal to the SAMD21 processor and can be updated via a Mobile Terminated (MT) SBD message.

### How do I install the ATSAMD21G18 bootloader?
Get yourself a Segger J-Link programmer and connect it according to [Atmel_SAMD21_Programming_Cable.pdf](https://github.com/PaulZC/Iridium_9603_Beacon/blob/master/Atmel_SAMD21_Programming_Cable.pdf).

Atmel_SAMD21_Programming_Cable

V5_Assembly_14

Ignore the RST connection.

Connect the 5V-Supply output from the J-Link to VBUS to power the board while you configure it (it doesn’t need external power for this bit).

Follow Lady Ada’s excellent instructions:
- https://learn.adafruit.com/proper-step-debugging-atsamd21-arduino-zero-m0/restoring-bootloader

If you are using Atmel's Studio:

Programming_1

Select Tools \ Device Programming

Programming_2

Select J-Link in the Tool pull-down menu
Select ATSAMD21G18A in the Device pull-down menu
Select SWD in the Interface pull-down menu
Then click Apply

Programming_2a

Click the J-Link icon to apply target power to the beacon

Programming_3

Select the Target Power tab and set Current State to Power On. This will apply 5V power from the J-Link
to the beacon VBUS

Programming_4

Close the J-Link window. In the Device Programming window click 'Read' to read the Device Signature and Target Voltage

Programming_5

Click 'Memories', click the '...' icon to select the bootloader Flash file
Click Program to erase, program and verify the device

Programming_6

Finally, select the J-Link icon again, select the Target Power tab and set Current State to Power Off
Close Device Programming and Atmel Studio and you are ready to configure the Beacon with the Arduino code

### How do I upload the Arduino code?
The 9603 Beacon is based on the Adafruit Feather M0 (Adalogger):
- https://www.adafruit.com/products/2796
- https://www.adafruit.com/products/2772

You can follow Lady Ada’s excellent instructions:
- https://cdn-learn.adafruit.com/downloads/pdf/adafruit-feather-m0-adalogger.pdf

### What other libraries do I need?
The main one is Mikal Hart’s Iridium SBD library (V2.0) written for the Rock7 RockBLOCK:
- http://arduiniana.org/libraries/iridiumsbd/
- https://github.com/mikalhart/IridiumSBD

The code uses Cristian Maglie's FlashStorage library to store and retrieve the BEACON_INTERVAL setting:
- https://github.com/cmaglie/FlashStorage

You will also need:
- https://github.com/mikalhart/TinyGPS
- http://arduiniana.org/libraries/pstring/
- https://github.com/adafruit/Adafruit_MPL3115A2_Library
- https://github.com/arduino-libraries/RTCZero
- https://github.com/adafruit/Adafruit_NeoPixel

## What data will I get back from the beacon?

The Arduino code included in this repository will send the following (separated by commas):
- GPS Time and Date (year, month, day, hour, minute, second)
- GPS Latitude (degrees)
- GPS Longitude (degrees)
- GPS Altitude (m)
- GPS Speed (m/s)
- GPS Heading (degrees)
- GPS HDOP (m)
- GPS Satellites
- Atmospheric pressure (Pa)
- Temperature (C)
- Battery / solar voltage (V)
- Iteration count

E.g.:

   _20170729144631,55.866573,-2.428458,103,0.1,0,3.0,5,99098,25.3,4.98,0_

You can opt to receive the data as an email attachment from the Iridium system. The email itself contains extra useful information:
- Message sequence numbers (so you can identify if any messages have been missed)
- The time and date the message session was processed by the Iridium system
- The status of the message session (was it successful or was the data corrupt)
- The size of the message in bytes
- The approximate latitude and longitude the message was sent from
- The approximate error radius of the transmitter’s location

E.g.:

   _From:	sbdservice@sbd.iridium.com_  
   _Sent:	20 August 2016 16:25_  
   _To:_  
   _Subject:	SBD Msg From Unit: 30043406174_  
   _Attachments:	30043406174-000029.sbd_  
  
   _MOMSN: 29_  
   _MTMSN: 0_  
   _Time of Session (UTC): Sat Aug 20 15:24:57 2016 Session Status: 00 - Transfer OK Message Size (bytes): 61_  
  
   _Unit Location: Lat = 55.87465 Long = -2.37135 CEPradius = 4_

You can adapt the code to send whatever data you like, up to a maximum of 340 bytes. The message is sent as plain text, but you could encrypt it if required.

You can opt to receive the data via HTTP instead of email. Your service provider will provide further details.

## Acknowledgements

I’m very grateful to Richard Meadows and his fellow students at UBSEDS (University of Bristol Students for the Exploration and Development of Space) who flew the V1 beacon on [UBSEDS22](http://www.bristol-seds.co.uk/hab/flight/2017/03/13/ubseds22.html).
- http://www.bristol-seds.co.uk/

I’m also very grateful to the UKHAS (UK High Altitude Society) team who provide the habhub flight tracker:
- https://ukhas.org.uk/
- http://tracker.habhub.org/

This project wouldn’t have been possible without the open source designs and code kindly provided by:
- Adafruit:

   The Adafruit SAMD Board library  
   The design for the Feather M0 Adalogger  
   For more details, check out the product page at:
   - https://www.adafruit.com/product/2772  

   Adafruit invests time and resources providing this open source design, please support Adafruit and open-source hardware by purchasing products from Adafruit!  
   Designed by Adafruit Industries.  
   Creative Commons Attribution, Share-Alike license

   The MPL3115A2 library
   The NeoPixel library

   Sercom examples:
   - https://learn.adafruit.com/using-atsamd21-sercom-to-add-more-spi-i2c-serial-ports/creating-a-new-serial

- Mikal Hart:

   The Iridium SBD library (distributed under the terms of the GNU LGPL license)  
   TinyGPS  
   PString

- Sparkfun:

   The MPL3115A2 Breakout:
   - https://www.sparkfun.com/products/11084

- Arduino:

   The Arduino IDE  
   Arduino SAMD Board library  
   RTCZero library

- Cave Moa:

   The SimpleSleepUSB example:
   - https://github.com/cavemoa/Feather-M0-Adalogger/tree/master/SimpleSleepUSB

- MartinL:

   Sercom examples:
   - https://forum.arduino.cc/index.php?topic=341054.msg2443086#msg2443086

- Cristian Maglie:

   FlashStorage library:
   - https://github.com/cmaglie/FlashStorage

## Licence

This project is distributed under a Creative Commons Share-alike 4.0 licence.
Please refer to section 5 of the licence for the "Disclaimer of Warranties and Limitation of Liability".

Enjoy!

**_Paul_**

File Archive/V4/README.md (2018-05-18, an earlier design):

# Iridium 9603N Beacon

A lightweight Iridium 9603N + GNSS Beacon (Tracker)

Suitable for high altitude ballooning, asset tracking and many other remote monitoring applications.

New hardware features for Version 4:
- Revised power options: solar; USB; or 3xAA battery
- u-blox MAX-M8Q GNSS with SMA antenna
- SMA antenna for the 9603N
- NeoPixel for status feedback
- Voltage reference so lower power voltages can be measured

New software features for Version 4:
- Beacon can be tracked from _anywhere_ with Iridium-Iridium messaging via the Rock7 RockBLOCK Gateway
- BEACON_INTERVAL is now stored in non-volatile (flash) memory
- BEACON_INTERVAL can be updated during a flight via a Mobile Terminated SBD message

Iridium_9603_Beacon_V4

**See [LEARN.md](https://github.com/PaulZC/Iridium_9603_Beacon/blob/master/Archive/V4/LEARN.md) for more details.**

**See [RockBLOCK.md](https://github.com/PaulZC/Iridium_9603_Beacon/blob/master/RockBLOCK.md) for details on how to track your beacon from _anywhere_ using Rock7 RockBLOCK Gateway messaging.**

See [Iridium_9603_Beacon_V4.pdf](https://github.com/PaulZC/Iridium_9603_Beacon/blob/master/Archive/V4/Iridium_9603_Beacon_V4.pdf) for the schematic, layout and Bill Of Materials.

The [Eagle](https://github.com/PaulZC/Iridium_9603_Beacon/tree/master/Archive/V4/Eagle) directory contains the schematic and pcb design files.

The [Arduino](https://github.com/PaulZC/Iridium_9603_Beacon/tree/master/Archive/V4/Arduino) directory contains the Arduino code.

The [Python](https://github.com/PaulZC/Iridium_9603_Beacon/tree/master/Python) directory contains tracking/mapping software based on the Google Static Maps API.

Mapper

This project is distributed under a Creative Commons Attribution + Share-alike (BY-SA) licence.
Please refer to section 5 of the licence for the “Disclaimer of Warranties and Limitation of Liability”.

Enjoy!

**_Paul_**

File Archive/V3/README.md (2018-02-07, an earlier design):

# Iridium 9603N Beacon

A lightweight Iridium 9603N + GNSS Beacon (Tracker)

Suitable for High Altitude Ballooning and many other remote monitoring applications.

Version 3 now includes u-blox SAM-M8Q GNSS and the option of solar power.

Iridium_9603_Beacon_V3

**See [LEARN.md](https://github.com/PaulZC/Iridium_9603_Beacon/blob/master/Archive/V3/LEARN.md) for more details.**

See [Iridium_9603_Beacon_V3.pdf](https://github.com/PaulZC/Iridium_9603_Beacon/blob/master/Archive/V3/Iridium_9603_Beacon_V3.pdf) for the schematic, layout and Bill Of Materials.

The [Eagle](https://github.com/PaulZC/Iridium_9603_Beacon/tree/master/Archive/V3/Eagle) directory contains the schematic and pcb design files.

The [Arduino](https://github.com/PaulZC/Iridium_9603_Beacon/tree/master/Archive/V3/Arduino) directory contains the Arduino code.

This project is distributed under a Creative Commons Attribution + Share-alike (BY-SA) licence.
Please refer to section 5 of the licence for the “Disclaimer of Warranties and Limitation of Liability”.

Enjoy!

**_Paul_**

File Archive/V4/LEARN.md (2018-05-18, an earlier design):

# Iridium 9603N Beacon

A lightweight Iridium 9603N + GNSS Beacon (Tracker)

Suitable for high altitude ballooning, asset tracking and many other remote monitoring applications.

New hardware features for Version 4:
- Revised power options: solar; USB; or 3xAA battery
- u-blox MAX-M8Q GNSS with SMA antenna
- SMA antenna for the 9603N
- NeoPixel for status feedback
- Voltage reference so lower power voltages can be measured

New software features for Version 4:
- Beacon can be tracked from _anywhere_ with Iridium-Iridium messaging via the Rock7 RockBLOCK Gateway
- BEACON_INTERVAL is now stored in non-volatile (flash) memory
- BEACON_INTERVAL can be updated during a flight via a Mobile Terminated SBD message

Iridium_9603_Beacon_V4

## Background

In response to feedback received from balloon enthusiasts, version 4 of the Iridium 9603N Beacon provides:
robust SMA antenna connections so helical antennas can be fitted to both the u-blox MAX-M8Q GNSS and Iridium 9603N;
extended battery power from three AA Energiser® Ultimate Lithium batteries;
a tri-colour NeoPixel LED for better status feedback.

Version 4 is slightly heavier than version 3. So, if you are looking for a very lightweight (60g) solar tracker for your long-duration high alitude balloon
flight, you might be better off with [version 3](https://github.com/PaulZC/Iridium_9603_Beacon/blob/master/Archive/V3/README.md). If you want a more robust
tracker for shorter-duration, battery-powered flights where the tracker stands a better chance of continuing to transmit while on the ground,
then version 4 is probably for you.

## The Design

See [Iridium_9603_Beacon_V4.pdf](https://github.com/PaulZC/Iridium_9603_Beacon/blob/master/Archive/V4/Iridium_9603_Beacon_V4.pdf) for the schematic,
layout and Bill Of Materials.

The [Eagle](https://github.com/PaulZC/Iridium_9603_Beacon/tree/master/Archive/V4/Eagle) directory contains the schematic and pcb design files.

Here's how the completed PCB looks when configured for USB power (using 1F super capacitors):




And here's how it looks from underneath when configured for battery power:

Iridium_9603_Beacon_V4_Bottom

The key components of V4 of the Iridium 9603N Beacon are:

### Iridium 9603N Module


Available from:
- https://www.rock7.com/shop-product-detail?productId=50

Other UK and International distributors can be found at:
- https://www.iridium.com/where-to-buy/?pid=27083

Make sure you purchase the 9603N and not the older 9603. The 9603N will run from 5V ± 0.5V which is important as the super capacitor charger is set to produce 5.3V; the older 9603 is only rated to 5V ± 0.2V.
If you do have the older 9603, you can change the super capacitor voltage to 4.8V by reconfiguring the split pads next to the super capacitors.



### SMA Iridium Antenna


An Iridium SMA helical antenna (e.g. the Maxtena M1621HCT-SMA, available from Farnell / Element 14 (2281619)) can be connected to the 9603N with a short Molex uFL cable (part number 73412-0508, available from Farnell / Element14 (1340201))

### Atmel ATSAMD21G18 Processor


As used on the Adafruit Feather M0:
- https://www.adafruit.com/products/2772

Available from e.g. Farnell / Element14 (2460544)

### MPL3115A2 Altitude/Pressure sensor:


As used on the Sparkfun SEN-11084
- https://www.sparkfun.com/products/11084

Available as a bare chip from e.g. Farnell / Element14 (2009084)

### Linear Technology LTC3225EDDB SuperCapacitor Charger


- http://www.linear.com/product/LTC3225

Available as a bare chip from e.g. Farnell / Element14 (1715231)

### u-blox MAX-M8Q GNSS


- https://www.u-blox.com/en/product/max-m8-series

Connect an antenna (e.g. the Maxtena M1516HCT-P-SMA, available from Farnell / Element 14 (2484960)) using the SMA connector. 3V power for an active antenna is provided.

### MCP111T-240 Reset Supervisor


The SAMD21G18 has a built-in power-on reset and brown-out detector circuit, but it doesn't work properly if the supply voltage rises very slowly.
The SAMD21G18 datasheet isn’t much help here. Section 8.2.4.1 specifies:
- _Minimum Rise Rate_

   _The integrated power-on reset (POR) circuitry monitoring the VDDANA power supply requires a minimum rise rate._

But then the supply characteristics section (37.4) specifies a _maximum_ supply rise rate of 0.1V/µs, not a minimum.

Tests I've carried out show that the processor will reset correctly if the power supply ramps up at 0.3 V/s or more, but fails to reset correctly at 0.2 V/s or less.
As the solar panel voltage will ramp up very slowly at sunrise, I've included a separate reset supervisor.
The Microchip MCP111-240 has an open drain output which holds the processor in reset until the supply rises above 2.4V, ensuring a clean start.

### SPX3819-3.3 Voltage Regulator


The SPX3819-3.3 Voltage Regulator regulates the output from the two solar panels, or the batteries, or the USB port, providing 3.3V for the processor, GNSS and pressure sensor.

The LTC3225EDDB SuperCapacitor Charger draws its power directly from the solar panels, batteries or USB without going through the regulator.

MBR120 diodes protect the solar panels, USB port and the batteries from each other.

### WS2812B "NeoPixel"


A tri-colour NeoPixel has been included on Version 4 to show the status of the beacon:
- Magenta at power up (loop_step == init) (~10 seconds)
- Blue when waiting for a GNSS fix (loop_step == start_GPS or read_GPS or read_pressure) (could take 5 mins)
- Cyan when waiting for supercapacitors to charge (loop_step == start_LTC3225 or wait_LTC3225) (could take 7 mins)
- White during Iridium transmit (loop_step == start_9603) (could take 5 mins)
- Green flash (2 seconds) indicates successful transmission
- Red flash (2 seconds) entering sleep
- LED will flash Red after: Iridium transmission (successful or failure); low battery detected; no GNSS data; supercapacitors failed to charge

### LT1634BCMS8-1.25 1.25V Voltage Reference


The SAMD21G18 processor is powered from a low drop-out 3.3V regulator. The solar / USB / battery voltage is measured via an analog pin connected to the mid point
of two 100K resistors configured as a voltage divider. The voltage measured by the analog pin is relative to the regulator voltage. When the power voltage drops below approximately
3.7V, the regulator voltage starts to collapse. The analog voltage appears to never drop below approximately 3.4V even when the actual voltage is lower than this.

By adding a 1.25V voltage reference and connecting it to a second analog pin, its constant voltage will appear to increase as the regulator voltage starts to collapse.
This voltage increase can be used to correct the power voltage measurement.

## How much does the V4 beacon weigh?

Configured for battery operation, including three Energiser® Ultimate Lithium AA batteries and the Maxtena SMA antennas listed in the BOM, it weighs 110.4g.



The weight breaks down as follows:
- Batteries: 45.3g
- Populated PCB with 1F supercapacitors and battery clips: 27.3g
- Iridium module with mounting hardware and uFL cable: 13.0g
- Iridium antenna: 12.5g
- GNSS antenna: 12.3g

Running from solar power, the total weight would be approximately 74g:
- Populated PCB with 10F supercapacitors: 25.0g
- Iridium module with mounting hardware and uFL cable: 13.0g
- Iridium antenna: 12.5g
- GNSS antenna: 12.3g
- Solar panels (2): 6.3g
- Support hardware for the solar panels: 5g

## Power Options 
V4 of the Iridium 9603N Beacon can draw power from: the solar panels; three AA batteries; or USB.
It is possible to connect all three or any two simultaneously, the beacon will simply draw power from whichever is providing the higher voltage.

If you are going to use solar power, use 10F super capacitors and a charge current of 60mA. Install the capacitors on the underside of the PCB, carefully
bending the legs to fit. Here is how they look on version 3 of the PCB:



If you are going to run exclusively from batteries or USB, then 1F super capacitors will suffice with the default charge current of 150mA.

The charge current can be changed by reconfiguring the split pads next to the super capacitors.



(The LTC3225 draws approximately _twice_ the chosen charge current. 300mA would be way too much for the PowerFilm solar panels.)

### Two PowerFilm Solar MPT3.6-150 solar panels




- http://www.powerfilmsolar.com/products/?mpt36150&show=product&productID=271537&productCategoryIDs=6573

Available (in the UK) from e.g.:
- http://www.selectsolar.co.uk/prod/264/powerfilm-mpt36150-100ma-36v-mini-solar-panel

You will want to angle the solar panels at +/- 45 degrees with respect to the circuit board so that at least one panel will collect sunlight while the sun is low in the sky.
When the sun is overhead, both panels will collect sunlight.

### Do the batteries really work at altitude?

Yes. Version 1 of the beacon was powered by three Energiser® Ultimate Lithium AAA batteries and sent updates
[from the UK all the way to China](https://github.com/PaulZC/Iridium_9603_Beacon/blob/master/Archive/V2/Iridium_9603_Beacon.pdf).

Here are the results of a 24 hour cold test on version 4 using dry ice. Messages were sent every 15 minutes. You can see that the AA battery voltage does vary with temperature
but at close to -40C the batteries are still providing ample voltage. There was still plenty of battery capacity remaining when I terminated the test after 24 hours (to save on message costs!).



### Do I need to be careful around the battery clips?

Yes! The clips are of course conductive. If you place the beacon battery-side down on a conductive surface **BAD THINGS WILL HAPPEN!**

### Why do you need the Super Capacitors?
The Iridium 9603 module draws an average current of 145mA and a peak current of 1.3A when transmitting its short data bursts. That’s too much for the solar panels to provide.
The LTC3225 super capacitor charger draws a lower current from the panels to slowly charge two 2.7V capacitors, connected in series, to 5.3V. The capacitors then deliver the 1.3A to the module when it sends the data burst.

### Why is the Super Capacitor Charger charge current set to 60mA / 150mA?
The datasheet for the 9603N quotes: an average idle current of 34mA; and an average receive current of 39mA.

For solar operation, we need to charge the capacitors at a higher current than 39mA, but keep the total current draw within what the solar panels can deliver.
(Remember that the LTC3225 draws approximately _twice_ the chosen charge current.)
The 10F capacitors provide the majority of the higher current draw during the transmit cycle.

For USB or battery operation, setting the super capacitor charge current to 150mA results in the capacitors only being needed to provide the 1.3A peak current when the 9603N is actually transmitting a data burst.
This means smaller (1F) capacitors are adequate.

### Can I leave the USB connected during testing?
Yes. Leaving the USB connected is useful as you can monitor the Serial messages produced by the code in the Arduino IDE Serial Monitor.
If you use a standard USB cable then the beacon will draw power from USB. To test the beacon running on solar power, you will need to break the USB 5V power connection.
You can do this with a home-made power-break cable.

Take a short male to female USB extension cable; carefully strip the outer sheath from cable somewhere near the middle;
prise apart the screen connection to reveal the four USB wires (red (5V); black (GND); green and white (data)); cut and insulate the ends of the red 5V wire leaving the black, green and white wires and the screen connection intact:



### Which AA batteries should I use?
Energiser® Ultimate Lithium batteries. These are rated down to -40°C but tests I’ve done (using dry ice) show that they continue to work much colder than that.
Please see the [V2 documentation](https://github.com/PaulZC/Iridium_9603_Beacon/blob/master/Archive/V2/Iridium_9603_Beacon.pdf) for further details.

## IO Pins


**SWCLK** and **SWDIO** are used during [programming of the SAMD bootloader](https://github.com/PaulZC/Iridium_9603_Beacon/blob/master/Archive/V2/LEARN.md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)

**3V3SW** is the 3.3V power rail switched by Q1 and which provides power for the MAX-M8Q GNSS and MPL3115A2 altitude sensor.
You can use this pin to provide power for a peripheral which you want to be able to disable to save power.

**SDA** and **SCL** are the I2C bus data and clock signals.
You can use these to connect another I2C sensor but be aware that it will share the bus with the MPL3115A2.

**3V3** is the 3.3V power rail from the SPX3819-3.3 voltage regulator.
Any peripherals connected to this will be continuously powered when power is available from the solar panels, batteries or USB.

**MISO**, **SCK**, **MOSI** and **SD_CS** are the SPI bus data, clock and enable connections.
You could use these to connect SD storage or another SPI peripheral.

## Do you recommend coating the board once it is populated?
As a minimum, I’d recommend applying a coat of acrylic protective lacquer to the processor and surrounding components (especially the crystal).
If you’re using an aerosol, be careful to mask off the connectors, switch and the pressure sensor first.

## Arduino Code
The [Arduino](https://github.com/PaulZC/Iridium_9603_Beacon/tree/master/Archive/V4/Arduino) directory contains the Arduino code.

The code is based extensively on Mikal Hart’s IridiumSBD Beacon example:
- https://github.com/mikalhart/IridiumSBD/tree/master/examples/Beacon

The main loop is structured around a large switch / case statement which:
- Initialises the serial ports; checks the solar panel voltage
- Powers up the GPS and MPL3115A2; checks the solar panel voltage
- Waits until the GPS establishes a fix; checks the solar panel voltage
- Reads the temperature and pressure from the MPL3115A2
- Powers down the GPS and powers up the LTC3225EDDB supercapacitor charger; checks the solar panel voltage
- Waits for the supercapacitors to charge; checks the solar panel voltage
- Queues the Iridium message transmission; checks the solar panel voltage
- Powers everything down and puts the processor to sleep until the next alarm interrupt

If the solar panel voltage falls below a useful level at any time, the code jumps to the sleep case and waits for the next alarm interrupt.

The BEACON_INTERVAL is stored in non-volatile (flash) memory internal to the SAMD21 processor and can be updated via a Mobile Terminated (MT) SBD message.

### How do I upload the Arduino code?
The 9603 Beacon is based on the Adafruit Feather M0 (Adalogger):
- https://www.adafruit.com/products/2796
- https://www.adafruit.com/products/2772

You can follow Lady Ada’s excellent instructions:
- https://cdn-learn.adafruit.com/downloads/pdf/adafruit-feather-m0-adalogger.pdf

### What other libraries do I need?
The main one is Mikal Hart’s Iridium SBD library (V2.0) written for the Rock7 RockBLOCK:
- http://arduiniana.org/libraries/iridiumsbd/
- https://github.com/mikalhart/IridiumSBD

The code uses Cristian Maglie's FlashStorage library to store and retrieve the BEACON_INTERVAL setting:
- https://github.com/cmaglie/FlashStorage

You will also need:
- https://github.com/mikalhart/TinyGPS
- http://arduiniana.org/libraries/pstring/
- https://github.com/adafruit/Adafruit_MPL3115A2_Library
- https://github.com/arduino-libraries/RTCZero
- https://github.com/adafruit/Adafruit_NeoPixel

### How do I install the ATSAMD21G18 bootloader?
Get yourself a Segger J-Link programmer and connect it according to [Atmel_SAMD21_Programming_Cable.pdf](https://github.com/PaulZC/Iridium_9603_Beacon/blob/master/Atmel_SAMD21_Programming_Cable.pdf).

Ignore the RST connection.

Connect the 5V-Supply output from the J-Link to VBUS to power the board while you configure it (it doesn’t need external power for this bit).

Follow Lady Ada’s excellent instructions:
- https://learn.adafruit.com/proper-step-debugging-atsamd21-arduino-zero-m0/restoring-bootloader

## What data will I get back from the beacon?

The Arduino code included in this repository will send the following (separated by commas):
- GPS Time and Date (year, month, day, hour, minute, second)
- GPS Latitude (degrees)
- GPS Longitude (degrees)
- GPS Altitude (m)
- GPS Speed (m/s)
- GPS Heading (degrees)
- GPS HDOP (m)
- GPS Satellites
- Atmospheric pressure (Pa)
- Temperature (C)
- Battery / solar voltage (V)
- Iteration count

E.g.:

   _20170729144631,55.866573,-2.428458,103,0.1,0,3.0,5,99098,25.3,4.98,0_

You can opt to receive the data as an email attachment from the Iridium system. The email itself contains extra useful information:
- Message sequence numbers (so you can identify if any messages have been missed)
- The time and date the message session was processed by the Iridium system
- The status of the message session (was it successful or was the data corrupt)
- The size of the message in bytes
- The approximate latitude and longitude the message was sent from
- The approximate error radius of the transmitter’s location

E.g.:

   _From:	sbdservice@sbd.iridium.com_  
   _Sent:	20 August 2016 16:25_  
   _To:_  
   _Subject:	SBD Msg From Unit: 30043406174_  
   _Attachments:	30043406174-000029.sbd_  
  
   _MOMSN: 29_  
   _MTMSN: 0_  
   _Time of Session (UTC): Sat Aug 20 15:24:57 2016 Session Status: 00 - Transfer OK Message Size (bytes): 61_  
  
   _Unit Location: Lat = 55.87465 Long = -2.37135 CEPradius = 4_

You can adapt the code to send whatever data you like, up to a maximum of 340 bytes. The message is sent as plain text, but you could encrypt it if required.

You can opt to receive the data via HTTP instead of email. Your service provider will provide further details.

## Acknowledgements

I’m very grateful to Richard Meadows and his fellow students at UBSEDS (University of Bristol Students for the Exploration and Development of Space) who flew the V1 beacon on [UBSEDS22](http://www.bristol-seds.co.uk/hab/flight/2017/03/13/ubseds22.html).
- http://www.bristol-seds.co.uk/

I’m also very grateful to the UKHAS (UK High Altitude Society) team who provide the habhub flight tracker:
- https://ukhas.org.uk/
- http://tracker.habhub.org/

This project wouldn’t have been possible without the open source designs and code kindly provided by:
- Adafruit:

   The Adafruit SAMD Board library  
   The design for the Feather M0 Adalogger  
   For more details, check out the product page at:
   - https://www.adafruit.com/product/2772  

   Adafruit invests time and resources providing this open source design, please support Adafruit and open-source hardware by purchasing products from Adafruit!  
   Designed by Adafruit Industries.  
   Creative Commons Attribution, Share-Alike license

   The MPL3115A2 library
   The NeoPixel library

   Sercom examples:
   - https://learn.adafruit.com/using-atsamd21-sercom-to-add-more-spi-i2c-serial-ports/creating-a-new-serial

- Mikal Hart:

   The Iridium SBD library (distributed under the terms of the GNU LGPL license)  
   TinyGPS  
   PString

- Sparkfun:

   The MPL3115A2 Breakout:
   - https://www.sparkfun.com/products/11084

- Arduino:

   The Arduino IDE  
   Arduino SAMD Board library  
   RTCZero library

- Cave Moa:

   The SimpleSleepUSB example:
   - https://github.com/cavemoa/Feather-M0-Adalogger/tree/master/SimpleSleepUSB

- MartinL:

   Sercom examples:
   - https://forum.arduino.cc/index.php?topic=341054.msg2443086#msg2443086

- Cristian Maglie:

   FlashStorage library:
   - https://github.com/cmaglie/FlashStorage

## Licence

This project is distributed under a Creative Commons Share-alike 4.0 licence.
Please refer to section 5 of the licence for the “Disclaimer of Warranties and Limitation of Liability”.

Enjoy!

**_Paul_**

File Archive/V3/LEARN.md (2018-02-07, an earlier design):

# Iridium 9603N Beacon

A lightweight Iridium 9603N + GNSS Beacon (Tracker)

Suitable for High Altitude Ballooning and many other remote monitoring applications.

Version 3 now includes u-blox SAM-M8Q GNSS and the option of solar power.

Iridium_9603_Beacon_V3

## Background

Following on from the [original work I did on the Iridium_9603_Beacon](https://github.com/PaulZC/Iridium_9603_Beacon/blob/master/Archive/V2/Iridium_9603_Beacon.pdf)
which got some nice coverage on [Hackaday](http://hackaday.com/2016/12/19/a-beacon-suitable-for-tracking-santas-sleigh/)
and which flew on [UBSEDS22](http://www.bristol-seds.co.uk/hab/flight/2017/03/13/ubseds22.html) and sent updates all the way from the UK to China before the batteries gave up:

UBSEDS22_KML
- https://github.com/PaulZC/Iridium_9603_Beacon/tree/master/UBSEDS22I_KML

I decided to set myself the challenge of modifying the design of the beacon to make it solar-powered, making the lithium batteries optional and allowing the beacon to send updates during daylight hours for as long as the balloon continues to float.
The design I’ve ended up with is based extensively on V2 of the Iridium 9603 Beacon but can now be powered by a pair of PowerFilm Solar MPT3.6-150 solar panels:
- http://www.powerfilmsolar.com/products/?mpt36150&show=product&productID=271537&productCategoryIDs=6573

These amazing little panels weigh only 3.1g each but can deliver a really useful amount of power: 100mA at 3.6V at Air Mass 1.5. This is enough to power the beacon’s SAMD21G18 processor and the GNSS receiver or the LTC3225EDDB super capacitor charger which delivers power to the Iridium 9603N.

The current status is that the V3 has worked successfully under full sun at sea level in the UK (during July) but hasn't flown yet.

I’ve tried to keep the beacon ‘general purpose’ and so you could use it for many other remote monitoring applications, perhaps relaying environmental data from remote locations using sensors connected to the I2C or SPI pins.

## The Design

See [Iridium_9603_Beacon_V3.pdf](https://github.com/PaulZC/Iridium_9603_Beacon/blob/master/Archive/V3/Iridium_9603_Beacon_V3.pdf) for the schematic,
layout and Bill Of Materials.

The [Eagle](https://github.com/PaulZC/Iridium_9603_Beacon/tree/master/Archive/V3/Eagle) directory contains the schematic and pcb design files.

Here's how the completed PCB looks when configured for solar power (using 10F super capacitors):




And here's how it looks from the side once the 9603N and antenna PCB have been mounted:



The key components of V3 of the Iridium 9603N Beacon are:

### Iridium 9603N Module



Available (in the UK) from e.g.:
- https://www.ast.systems/unitedkingdom/products/product/iridium-9603-sbd-short-burst-data-transceiver/
- http://www.rock7mobile.com/products-iridium-sbd

Other UK and International distributors can be found at:
- https://iridium.com/products/details/Iridium-9603?section=wtb 

Make sure you purchase the 9603N and not the older 9603. The 9603N will run from 5V ± 0.5V which is important as the super capacitor charger is set to produce 5.3V; the older 9603 is only rated to 5V ± 0.2V.

### Taoglas IP.1621.25.4.A.021 Iridium Patch Antenna


Available from e.g. Mouser (Part# 960-IP1621254A02)

This is mounted on a small PCB above the 9603N:
- https://github.com/PaulZC/Iridium_9603_Beacon/blob/master/Archive/V3/Eagle/Iridium_9603_Antenna.brd

and is connected to the 9603N with a short Molex uFL cable (part number 73412-0508, available from Farnell / Element14 (1340201))

### Atmel ATSAMD21G18 Processor


As used on the Adafruit Feather M0:
- https://www.adafruit.com/products/2772

Available from e.g. Farnell / Element14 (2460544)

### MPL3115A2 Altitude/Pressure sensor:


As used on the Sparkfun SEN-11084
- https://www.sparkfun.com/products/11084

Available as a bare chip from e.g. Farnell / Element14 (2009084)

### Linear Technology LTC3225EDDB SuperCapacitor Charger


- http://www.linear.com/product/LTC3225

Available as a bare chip from e.g. Farnell / Element14 (1715231)

Charges two e.g. Bussmann HV1030-2R7106-R 10F 2.7V capacitors (Farnell / Element14 2148486)



### u-blox SAM-M8Q GNSS


- https://www.u-blox.com/en/product/sam-m8q-module

### Two PowerFilm Solar MPT3.6-150 solar panels




- http://www.powerfilmsolar.com/products/?mpt36150&show=product&productID=271537&productCategoryIDs=6573

Available (in the UK) from e.g.:
- http://www.selectsolar.co.uk/prod/264/powerfilm-mpt36150-100ma-36v-mini-solar-panel

You will want to angle the solar panels at +/- 45 degrees with respect to the circuit board so that at least one panel will collect sunlight while the sun is low in the sky.
When the sun is overhead, both panels will collect sunlight.

Iridium_9603_Beacon_V3



### MCP111T-240 Reset Supervisor


The SAMD21G18 has a built-in power-on reset and brown-out detector circuit, but it doesn't work properly if the supply voltage rises very slowly.
The SAMD21G18 datasheet isn’t much help here. Section 8.2.4.1 specifies:
- _Minimum Rise Rate_

   _The integrated power-on reset (POR) circuitry monitoring the VDDANA power supply requires a minimum rise rate._

But then the supply characteristics section (37.4) specifies a _maximum_ supply rise rate of 0.1V/µs, not a minimum.

Tests I've carried out show that the processor will reset correctly if the power supply ramps up at 0.3 V/s or more, but fails to reset correctly at 0.2 V/s or less.
As the solar panel voltage will ramp up very slowly at sunrise, I've included a separate reset supervisor.
The Microchip MCP111-240 has an open drain output which holds the processor in reset until the supply rises above 2.4V, ensuring a clean start.

### SPX3819-3.3 Voltage Regulator


The SPX3819-3.3 Voltage Regulator regulates the output from the two solar panels, or the batteries, or the USB port, providing 3.3V for the processor, GNSS and pressure sensor.

The LTC3225EDDB SuperCapacitor Charger draws its power directly from the solar panels, batteries or USB without going through the regulator.

MBR120 diodes protect the solar panels and the batteries from each other, and when the PCB is connected to USB.

## Power Options 
V3 of the Iridium 9603N Beacon can draw power from: the solar panels; three AAA batteries; or USB.
It is possible to connect both the solar panels and the batteries, the beacon will simply draw power from whichever is providing the higher voltage.

If you are going to use solar power, use the 10F super capacitors described above.

If you are going to run exclusively from batteries or USB, then 1F super capacitors will suffice if you increase the super capacitor charge current to 150mA.
Do this by replacing R2 with a 12K resistor instead of 30K. Remember that this would be too much for the solar panels. (The LTC3225 draws approximately _twice_ the chosen charge current.)

The BOM lists the different parts you'll need for the two configurations. Here are images of V1 of the beacon configured for batteries plus 1F capacitors:





 
### Why do you need the Super Capacitors?
The Iridium 9603 module draws an average current of 145mA and a peak current of 1.3A when transmitting its short data bursts. That’s too much for the solar panels to provide.
The LTC3225 super capacitor charger draws a lower current from the panels to slowly charge two 10F 2.7V capacitors, connected in series, to 5.3V. The capacitors then deliver the 1.3A to the module when it sends the data burst.

### Why is the Super Capacitor Charger charge current set to 60mA?
The datasheet for the 9603N quotes: an average idle current of 34mA; and an average receive current of 39mA.
We need to charge the capacitors at a higher current than this, but keep the total current draw within what the solar panels can deliver.
(Remember that the LTC3225 draws approximately _twice_ the chosen charge current.)

### Can I leave the USB connected during testing?
Yes. Leaving the USB connected is useful as you can monitor the Serial messages produced by the code in the Arduino IDE Serial Monitor.
If you use a standard USB cable then the beacon will draw power from USB. To test the beacon running on solar power, you will need to break the USB 5V power connection.
You can do this with a home-made power-break cable.

Take a short male to female USB extension cable; carefully strip the outer sheath from cable somewhere near the middle;
prise apart the screen connection to reveal the four USB wires (red (5V); black (GND); green and white (data)); cut and insulate the ends of the red 5V wire leaving the black, green and white wires and the screen connection intact:



### Which AAA batteries should I use?
Energiser® Ultimate Lithium batteries. These are rated down to -40°C but tests I’ve done (using dry ice) show that they continue to work much colder than that.
Please see the [V2 documentation](https://github.com/PaulZC/Iridium_9603_Beacon/blob/master/Archive/V2/Iridium_9603_Beacon.pdf) for further details.

## IO Pins


**SWCLK** and **SWDIO** are used during [programming of the SAMD bootloader](https://github.com/PaulZC/Iridium_9603_Beacon/blob/master/Archive/V3/LEARN.md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)

**3V3SW** is the 3.3V power rail switched by Q1 and which provides power for the SAM-M8Q GNSS and MPL3115A2 altitude sensor.
You can use this pin to provide power for a peripheral which you want to be able to disable to save power.

**SDA** and **SCL** are the I2C bus data and clock signals.
You can use these to connect another I2C sensor but be aware that it will share the bus with the MPL3115A2.

**3V3** is the 3.3V power rail from the SPX3819-3.3 voltage regulator.
Any peripherals connected to this will be continuously powered when power is available from the solar panels, batteries or USB.

**MISO**, **SCK**, **MOSI** and **SD_CS** are the SPI bus data, clock and enable connections.
You could use these to connect SD storage or another SPI peripheral.

## Do you recommend coating the board once it is populated?
As a minimum, I’d recommend applying a coat of acrylic protective lacquer to the processor and surrounding components (especially the crystal).
If you’re using an aerosol, be careful to mask off the connectors, switch and the pressure sensor first.

## Arduino Code
The [Arduino](https://github.com/PaulZC/Iridium_9603_Beacon/tree/master/Archive/V3/Arduino) directory contains the Arduino code.

The code is based extensively on Mikal Hart’s IridiumSBD Beacon example:
- https://github.com/mikalhart/IridiumSBD/tree/master/examples/Beacon

The main loop is structured around a large switch / case statement which:
- Initialises the serial ports; checks the solar panel voltage
- Powers up the GPS and MPL3115A2; checks the solar panel voltage
- Waits until the GPS establishes a fix; checks the solar panel voltage
- Reads the temperature and pressure from the MPL3115A2
- Powers down the GPS and powers up the LTC3225EDDB supercapacitor charger; checks the solar panel voltage
- Waits for the supercapacitors to charge; checks the solar panel voltage
- Queues the Iridium message transmission; checks the solar panel voltage
- Powers everything down and puts the processor to sleep until the next alarm interrupt

If the solar panel voltage falls below a useful level at any time, the code jumps to the sleep case and waits for the next alarm interrupt.

### How do I upload the Arduino code?
The 9603 Beacon is based on the Adafruit Feather M0 (Adalogger):
- https://www.adafruit.com/products/2796
- https://www.adafruit.com/products/2772

You can follow Lady Ada’s excellent instructions:
- https://cdn-learn.adafruit.com/downloads/pdf/adafruit-feather-m0-adalogger.pdf

### What other libraries do I need?
The main one is Mikal Hart’s Iridium SBD library (V2.0) written for the Rock7 RockBLOCK:
- http://arduiniana.org/libraries/iridiumsbd/
- https://github.com/mikalhart/IridiumSBD

You will also need:
- https://github.com/mikalhart/TinyGPS
- http://arduiniana.org/libraries/pstring/
- https://github.com/adafruit/Adafruit_MPL3115A2_Library
- https://github.com/arduino-libraries/RTCZero

### How do I install the ATSAMD21G18 bootloader?
Get yourself a Segger J-Link programmer and connect it according to [Atmel_SAMD21_Programming_Cable.pdf](https://github.com/PaulZC/Iridium_9603_Beacon/blob/master/Atmel_SAMD21_Programming_Cable.pdf).

Ignore the RST connection.

Connect the 5V-Supply output from the J-Link to one of the SOLAR+ connections to power the board while you configure it (it doesn’t need batteries or solar power for this bit).

Follow Lady Ada’s excellent instructions:
- https://learn.adafruit.com/proper-step-debugging-atsamd21-arduino-zero-m0/restoring-bootloader

## What data will I get back from the beacon?

The Arduino code included in this repository will send the following (separated by commas):
- GPS Time and Date (year, month, day, hour, minute, second)
- GPS Latitude (degrees)
- GPS Longitude (degrees)
- GPS Altitude (m)
- GPS Speed (m/s)
- GPS Heading (degrees)
- GPS HDOP (m)
- GPS Satellites
- Atmospheric pressure (Pa)
- Temperature (C)
- Battery / solar voltage (V)
- Iteration count

E.g.:

   _20170729144631,55.866573,-2.428458,103,0.1,0,3.0,5,99098,25.3,4.98,0_

You can opt to receive the data as an email attachment from the Iridium system. The email itself contains extra useful information:
- Message sequence numbers (so you can identify if any messages have been missed)
- The time and date the message session was processed by the Iridium system
- The status of the message session (was it successful or was the data corrupt)
- The size of the message in bytes
- The approximate latitude and longitude the message was sent from
- The approximate error radius of the transmitter’s location

E.g.:

   _From:	sbdservice@sbd.iridium.com_  
   _Sent:	20 August 2016 16:25_  
   _To:_  
   _Subject:	SBD Msg From Unit: 30043406174_  
   _Attachments:	30043406174-000029.sbd_  
  
   _MOMSN: 29_  
   _MTMSN: 0_  
   _Time of Session (UTC): Sat Aug 20 15:24:57 2016 Session Status: 00 - Transfer OK Message Size (bytes): 61_  
  
   _Unit Location: Lat = 55.87465 Long = -2.37135 CEPradius = 4_

You can adapt the code to send whatever data you like, up to a maximum of 340 bytes. The message is sent as plain text, but you could encrypt it if required.

You can opt to receive the data via HTTP instead of email. Your service provider will provide further details.

## Acknowledgements

I’m very grateful to Richard Meadows and his fellow students at UBSEDS (University of Bristol Students for the Exploration and Development of Space) who flew the V1 beacon on [UBSEDS22](http://www.bristol-seds.co.uk/hab/flight/2017/03/13/ubseds22.html).
- http://www.bristol-seds.co.uk/

I’m also very grateful to the UKHAS (UK High Altitude Society) team who provide the habhub flight tracker:
- https://ukhas.org.uk/
- http://tracker.habhub.org/

This project wouldn’t have been possible without the open source designs and code kindly provided by:
- Adafruit:

   The Adafruit SAMD Board library  
   The design for the Feather M0 Adalogger  
   For more details, check out the product page at:
   - https://www.adafruit.com/product/2772  

   Adafruit invests time and resources providing this open source design, please support Adafruit and open-source hardware by purchasing products from Adafruit!  
   Designed by Adafruit Industries.  
   Creative Commons Attribution, Share-Alike license

   The MPL3115A2 library

   Sercom examples:
   - https://learn.adafruit.com/using-atsamd21-sercom-to-add-more-spi-i2c-serial-ports/creating-a-new-serial

- Mikal Hart:

   The Iridium SBD library (distributed under the terms of the GNU LGPL license)  
   TinyGPS  
   PString

- Sparkfun:

   The MPL3115A2 Breakout:
   - https://www.sparkfun.com/products/11084

- Arduino:

   The Arduino IDE  
   Arduino SAMD Board library  
   RTCZero library

- Cave Moa:

   The SimpleSleepUSB example:
   - https://github.com/cavemoa/Feather-M0-Adalogger/tree/master/SimpleSleepUSB

- MartinL:

   Sercom examples:
   - https://forum.arduino.cc/index.php?topic=341054.msg2443086#msg2443086

## Licence

This project is distributed under a Creative Commons Share-alike 4.0 licence.
Please refer to section 5 of the licence for the “Disclaimer of Warranties and Limitation of Liability”.

Enjoy!

**_Paul_**

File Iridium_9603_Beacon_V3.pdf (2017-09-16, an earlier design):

A

A


01/08/2017 23:13 \\thunderbird\home\pclark\Documents\eagle\Iridium_9603_Beacon\V3\Iridium_9603_Beacon.sch (Sheet: 1/6)

A

A

OUT 5; GND 2; GND 18*4; VDDA 6; PA16/I2C/I0/SERCOM1+3.0; PA17/I2C/I1/SERCOM1+3.1; PA18/I2/SERCOM1+3.2; PA19/I3/SERCOM1+3.3/I2SD0; PA22/I2C/I6/SERCOM3+5.0; PA23/I2C/I7/SERCOM3+5.1/SOF; PA24/I12/SERCOM3+5.2/D-; PA25/I13/SERCOM3+5.3/D+; PA30/I10/SECOM1.2/SWCLK; PA31/I11/SECOM1.3/SWDIO; PA09/I2C/I9/AIN17/SERCOM0+2.1/I2SMC; 14 PA08/I2C/AIN16/SERCOM0+2.0/I2SD1; PA15/I15/SERCOM3+4.3; PA11/I11/AIN19/SERCOM0+2.3/I2SF0; PA14/I14/SERCOM2+4.2; PA10/I10/AIN18/SERCOM0+2.2/I2SCK; /RESET 40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

01/08/2017 23:13 \\thunderbird\home\pclark\Documents\eagle\Iridium_9603_Beacon\V3\Iridium_9603_Beacon.sch (Sheet: 2/6)

A

A

VCC_IO 2; V_BCKP 3; GND 1*9; SAFEBOOT_N 8; SDA 9; SCL; TXD; RXD; VCC 17; RESET_N 18; EXTINT 19

01/08/2017 23:13 \\thunderbird\home\pclark\Documents\eagle\Iridium_9603_Beacon\V3\Iridium_9603_Beacon.sch (Sheet: 3/6)

VDD 1 CAP 2 GND 3 VDDIO 4; SCL; SDA; INT1; INT2

01/08/2017 23:13 \\thunderbird\home\pclark\Documents\eagle\Iridium_9603_Beacon\V3\Iridium_9603_Beacon.sch (Sheet: 4/6)

A

A

VIN 9; CX 3 ~SHDN 4 VSEL 6 PROG 7; GND_2 11 GND 8; COUT; PGOOD

01/08/2017 23:13 \\thunderbird\home\pclark\Documents\eagle\Iridium_9603_Beacon\V3\Iridium_9603_Beacon.sch (Sheet: 5/6)

A

A


01/08/2017 23:13 \\thunderbird\home\pclark\Documents\eagle\Iridium_9603_Beacon\V3\Iridium_9603_Beacon.sch (Sheet: 6/6)


18/04/2017 09:37 \\thunderbird\home\pclark\Documents\eagle\Iridium_9603_Beacon\V3\Iridium_9603_Beacon.brd


Part X | Y | Angle Package Value | Manufacturer | Manufacturer Part No

Farnell Part
No | Mouser Part No | Description
FD1 | 7.62 | 12.7 | 0 | | | | | | Fiducial
FD2 | 43.18 | 58.42 | 0 | | | | | | Fiducial
C1 | 26.99 | 24.51 | 180 | 0603 | 1uF | Walsin | 0603X105K100CT | 2496916 | MultiLayer Ceramic Capacitor; 1uF; 10V; 0603; X5R
C2 | 37.47 | 27.05 | 0 | 0603 | 12pF | Walsin | 0603N120J500CT | 2496884 | MultiLayer Ceramic Capacitor; 12pF; 50V; 0603
C3 | 12.76 | 35.81 | 270 | 0805 | 10uF | Walsin | 0805F106Z100CT | 2496998 | MultiLayer Ceramic Capacitor; 10uF; 10V; 0805
C4 | 37.47 | 29.53 | 0 | 0603 | 12pF | Walsin | 0603N120J500CT | 2496884 | MultiLayer Ceramic Capacitor; 12pF; 50V; 0603
C5 | 32.7 | 38.48 | 180 | 0805 | 10uF | Walsin | 0805F106Z100CT | 2496998 | MultiLayer Ceramic Capacitor; 10uF; 10V; 0805
C6 | 9.21 | 24.77 | 270 | 0805 | 10uF | Walsin | 0805F106Z100CT | 2496998 | MultiLayer Ceramic Capacitor; 10uF; 10V; 0805
C7 | 20.32 | 24.77 | 270 | 0603 | 1uF | Walsin | 0603X105K100CT | 2496916 | MultiLayer Ceramic Capacitor; 1uF; 10V; 0603; X5R
C8 | 18.1 | 24.77 | 270 | 0805 | 10uF | Walsin | 0805F106Z100CT | 2496998 | MultiLayer Ceramic Capacitor; 10uF; 10V; 0805
C9 | 11.75 | 38.73 | 0 | 0805 | 0.1uF | Walsin | 0805B104K500CT | 2496944 | MultiLayer Ceramic Capacitor; 0.1uF; 50V; 0805; X7R
C10 | 15.56 | 45.09 | 0 | 0805 | 10uF | Walsin | 0805F106Z100CT | 2496998 | MultiLayer Ceramic Capacitor; 10uF; 10V; 0805
C13 | 13.46 | 32.64 | 0 | 0603 | 0.1uF | Walsin | 0603B104K500CT | 2496834 | MultiLayer Ceramic Capacitor; 0.1uF; 50V; 0603; X7R
C14 | 35.37 | 32.19 | 0 | 0603 | 1uF | Walsin | 0603X105K100CT | 2496916 | MultiLayer Ceramic Capacitor; 1uF; 10V; 0603; X5R
C15 | 34.1 | 40.7 | 0 | 0603 | 1uF | Walsin | 0603X105K100CT | 2496916 | MultiLayer Ceramic Capacitor; 1uF; 10V; 0603; X5R
C16 | 33.27 | 47.31 | 0 | 0603 | 0.22uF | Multicomp | MC0603F224Z160CT | 1759019 | MultiLayer Ceramic Capacitor; 0.22uF; 16V; 0603
C17 | 33.37 | 55.66 | 0 | 0805 | 2.2uF | Multicomp | MCTT21X225K100CT | 1759477 | MultiLayer Ceramic Capacitor; 2.2uF; 10V; 0805; X5R
CON1 29.34 | 8.07 | 0 | Micro_USB | Amphenol_FCI | 10103594 | 2293752 | Amphenol FCI 10103594 Micro USB Type B
D1 | 4.73 | 49.56 | 90 | SOD-123 MBR120 | ON SEMICONDUCTOR | MBR120VLSFT1G | 1431044 | Schottky Rectifier; 20V; 1A; SOD-123
D2 | 4.7 | 23.18 | 180 | SOD-123 MBR120 | ON SEMICONDUCTOR | MBR120VLSFT1G | 1431044 | Schottky Rectifier; 20V; 1A; SOD-123
D3 | 2.54 | 49.53 | 90 | SOD-123 MBR120 | ON SEMICONDUCTOR | MBR120VLSFT1G | 1431044 | Schottky Rectifier; 20V; 1A; SOD-123
J1 | 22.78 | 42.71 | 0 | | SS4-10-3.50 | Samtec | SS4-10-3.50-L-D-K-TR | 2085336 | Samtec SS4-10-3.50-L-D-K-TR
LED1 19.05 | 8.57 | 180 | 2.0x1.25 RED | Multicomp | 703-0107 | 2112119 | LED; Red; 20mA; 2.2V; 2.0x1.25mm
Q1 | 11.75 | 42.55 | 90 | SOT23 | DMG3415U-7 | Diodes Inc. | DMG3415U-7 | 1843688 | MOSFET; P Channel; SOT23-WIDE
R1 | 16.45 | 39.62 | 90 | 0805 | 100k | Multicomp | MC01W08051100K | 9332405 | Chip Resistor; Thick Film; 100k; 150V; 0805; 100mW
R2 | 39.43 | 45.02 | 90 | 0805 | 30k | Panasonic | ERJ6GEYJ303V | 2323834 | Chip Resistor; Thick Film; 30k; 150V; 0805; 125 mW
R3 | 33.69 | 24.26 | 0 | 0603 | 100k | Yageo | RC0603FR-13100KL | 2309107 | Chip Resistor; Thick Film; 100k; 50V; 0603; 100mW
R4 | 38.42 | 40.58 | 0 | 0805 | 100k | Multicomp | MC01W08051100K | 9332405 | Chip Resistor; Thick Film; 100k; 150V; 0805; 100mW
R5 | 13.46 | 30.45 | 0 | 0603 | 1K | Multicomp | MCWR06X1001FTL | 2447272 | Chip Resistor; Thick Film; 1k; 50V; 0603; 100mW
R6 | 37.5 | 24.26 | 0 | 0603 | 100k | Yageo | RC0603FR-13100KL | 2309107 | Chip Resistor; Thick Film; 100k; 50V; 0603; 100mW
R7 | 19.05 | 12.7 | 270 | 0603 | 2.2K | Panasonic | ERJ3GEYJ222V | 2059610 | Chip Resistor; Thick Film; 2.2k; 75V; 0603; 100mW
R8 | 9.27 | 30.45 | 180 | 0603 | 1K | Multicomp | MCWR06X1001FTL | 2447272 | Chip Resistor; Thick Film; 1k; 50V; 0603; 100mW
SW1 22.54 | 8.89 | 270 | 4.6x2.8 | Tactile Switch | Multicomp | MCIPTG23K-V | 1605470 | Tactile Switch; 4.6x2.8mm; 50mA; 12V
U1 | 27.05 | 20.83 | 0 | SOT23-3 MCP111T-240E/TT Microchip | MCP111T-240E/TT | 1627192 | Reset Supervisor; SOT23-3; 2.40V; Open Drain; Active Low
U2 | 14.29 | 24.77 | 270 | SOT23-5 SPX3819-3.3 | Exar | SPX3819M5-L-3-3/TR | 701-SPX3819M5-L-33TR | LDO Voltage Regulator; 500mA; SOT-23-5
U3 | 35.56 | 43.62 | 90 | DFN-10 | LTC3225EDDB | Linear Technology | LTC3225EDDB#TRMPBF | 1715231 | Supercapacitor Charger
U4 | 8.54 | 34.29 | 180 | LGA8 | MPL3115A2 | NXP | MPL3115A2 | 2009084 | Pressure Sensor
U5 | 26.99 | 30.86 | 90 | TQFN48 ATSAMD21G18A | Atmel | ATSAMD21G18A-MF | 2460544 | ATSAMD21G18A-MF; QFN48
U6 | 15.18 | 57.02 | 270 | | SAM-M8Q | u-blox | SAM-M8Q | | https://www.u-blox.com/en/product/sam-m8q-module
X1 | 34.16 | 28.32 | 270 | 3.2x1.5 | 32.768 | Epson | Q13FC13500004 | 1278036 | Crystal; 32.768kHz; 12.5pF; 3.2 x 1.5mm

Part | Value | Manufacturer | Manufacturer Part No | Farnell Part
No | Mouser Part No
| | | | McMaster
| | | | Part No | Description

Non-surface mount components:
BAT1 | AAA-Clip_Pair | Keystone Electronics | 82 | 908721 | Keystone Electronics 82 AAA Battery Clip (Pair)
BAT2 | AAA-Clip_Pair | Keystone Electronics | 82 | 908721 | Keystone Electronics 82 AAA Battery Clip (Pair)
BAT3 | AAA-Clip_Pair | Keystone Electronics | 82 | 908721 | Keystone Electronics 82 AAA Battery Clip (Pair)
C11 | 1F 2.7V | Bussmann | HV0810-2R7105-R | 2148482 | Supercapacitor; 1F; 2.7V; +30%, -10%; 3.5mm Pitch
C12 | 1F 2.7V | Bussmann | HV0810-2R7105-R | 2148482 | Supercapacitor; 1F; 2.7V; +30%, -10%; 3.5mm Pitch
S1 | Press-In Nut | McMaster-Carr | 95117A411 | 95117A411 | Press-In Nut; 2-56
S2 | Press-In Nut | McMaster-Carr | 95117A411 | 95117A411 | Press-In Nut; 2-56

Mounting hardware for Iridium 9603N and antenna PCB:
SPACERS_x4 | | | | 94669A100 | 4.5mm OD x 6mm Spacers for Iridium Module and Antenna PCB
SCREWS_x2 | | | | 92185A092 | 2-56 x 0.75" Screws for Iridium Module and Antenna PCB

Components for antenna PCB:
ANT1 | IP.1621.25.4.A.02 Taoglas | IP.1621.25.4.A.02 | 960-IP1621254A02 | 25mm Iridium Patch Antenna
X1 | uFL | Hirose | U.FL-R-SMT(01) | 3908021 | HIROSE U.FL-R-SMT(01); U.FL Coaxial; Straight Jack; 50 ohm
CABLE | | Molex | 73412-0508 | 1340201 | Molex uFL Plug/Plug 50mm 73412-0508

For solar operation:
Don't install BAT1-BAT3 battery clips
Replace C11 and C12 with 10F capacitors. Install these flat against the underside of the PCB, carefully bending the legs to fit.
C11 & C12 | 10F 2.7V | Bussmann | HV1030-2R7106-R | 2148486 | Supercapacitor; 10F; 2.7V; +30%, -10%; 5.0mm Pitch
Connect two PowerFilm MPT3.6-150 solar panels to the SOLAR+/- terminals. Be careful with the panel polarity.

SOLAR2+ | SOLAR1+


SOLAR2- | SOLAR1-

# Iridium 9603N Beacon V3

# Connected to: 2 x PowerFilm Solar MPT3.6-150

# Note Panel Orientation!

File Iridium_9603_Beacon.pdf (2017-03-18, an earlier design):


+

Iridium 9603 Beacon
(Updated March 18th 2017)

=

Background:
One of the more unusual projects I’ve been involved with is “BIT” – the Balloon-borne Imaging Telescope: a 0.5m telescope flown below a large balloon at an altitude of 30km, above 99% of the Earth’s atmosphere. The project is being led by the University of Toronto and Princeton University. You can find out more about the project at: https://sites.physics.utoronto.ca/bit/
There is a nice time lapse and video montage of the 2016 “SuperBIT” flight from CSBF, Palestine, Texas here:
https://www.youtube.com/watch?v=jsKrfpdGslg
and here is a nice press release about the 2015 BIT flight from Timmins, Canada: http://www.asc-csa.gc.ca/eng/blog/2016/03/31/university-of-toronto-students-send-a-telescope-soaring-through-the-stratosphere.asp (http://www.asc-csa.gc.ca/eng/blog/2016/03/31/university-of-toronto-students-send-a-telescope-soaring-through-the-stratosphere.asp)
Now, one of the tricky parts of high altitude balloon missions is that you are not guaranteed to get your balloon payload back again, especially with launches from places like New Zealand where most of the flight takes place over the sea. Wouldn’t it be great if you could ‘drop off’ some of the precious scientific data each time the balloon passes over land? Well, we’ve been investigating exactly that and working out what it would take for a small, autonomous glider – essentially a flying hard drive – to navigate from 30km to a drop zone somewhere near a major road.
One of the essential components for the glider will be a “come get me” location beacon, so it can tell us where it is and allow us to pick it up once it has landed. The design I have been testing uses an Iridium 9603 Short Burst Data module, which can transmit short (email) messages from anywhere on Earth via the Iridium® satellite network. I included a GPS receiver so the beacon can transmit its location, an altitude/pressure and temperature sensor, and powered the beacon from AAA Energiser Ultimate Lithium batteries which are able to withstand the -60°C temperatures encountered during the flight.
The design I’ve ended up with weighs in at 72.6g and is light enough to fly on a much smaller balloon should you want to.
I’ve tried to keep the beacon ‘general purpose’ and so you could use it for many other remote monitoring applications, perhaps relaying environmental data from remote locations using sensors connected to the I2C or SPI pins.

Have you flown one of these beacons?
Yes! Richard Meadows and his fellow students at UBSEDS (University of Bristol Students for the Exploration and Development of Space) kindly launched one of my beacons on Monday March 13th 2017. They used a small super-pressure helium balloon constructed from food packaging film, a multi-layer material containing PA (Polyamide aka. Nylon), EVOH and PE (Polythene) with a total thickness of 20 - 60 µm. They constructed the balloon themselves by carefully heat-welding sheets of the film together. I am very grateful for all of their hard work.
At the time of writing the balloon is still flying. You can track the Iridium fixes using the wonderful UKHAS habhub tracker: https://tracker.habhub.org/#!mt=roadmap&mz=11&qm=3_days&f=UBSEDS22I
You can find more details about the flight here (altitude data is provided by a UBSEDS solar-powered radio tracker travelling on the same flight): http://www.bristol-seds.co.uk/hab/flight/2017/03/13/ubseds22.html
You can find Google Earth KML files for the flight in: https://github.com/PaulZC/Iridium_9603_Beacon/tree/master/UBSEDS22I_KML

Tell me about the design:
You can find background information about the prototype for the beacon at: https://github.com/PaulZC/Iridium_9603_Beacon_Prototype
The key components of the finished beacon are:
- Iridium 9603 Module
- Available (in the UK) from e.g.:
- http://www.ast-systems.co.uk/Product-Pages/Iridium-9603-SBD— Satellite-Tracking-Transceiver.aspx (http://www.ast-systems.co.uk/Product-Pages/Iridium-9603-SBD--Satellite-Tracking-Transceiver.aspx)
- http://www.rock7mobile.com/products-iridium-sbd
- Other UK and International distributors can be found at:
- https://iridium.com/products/details/Iridium-9603?section=wtb
- Taoglas IP.1621.25.4.A.021 Iridium Patch Antenna
- Available from e.g. Mouser (960-IP1621254A02)
- Atmel ATSAMD21G18 Processor
- As used on the Adafruit Feather M0:

- https://www.adafruit.com/products/2772
- Available from e.g. Farnell / Element14 (2460544)
- GlobalTop FGPMMOPA6H GPS module
- As used on the Adafruit Ultimate GPS:
- https://www.adafruit.com/products/790
- MPL3115A2 Altitude/Pressure sensor:
- As used on the Sparkfun SEN-11084
- https://www.sparkfun.com/products/11084
- Available as a bare chip from e.g. Farnell / Element14 (2009084)
- Linear Technology LTC3225EDDB SuperCapacitor Charger
- http://www.linear.com/product/LTC3225
- Available as a bare chip from e.g. Farnell / Element14 (1715231)
- Charges two e.g. Bussmann HV0810-2R7105-R 1F 2.7V capacitors (Farnell / Element14 2148482)
You can find the full schematics, overlays and bill of materials in: Iridium_9603_Beacon_V2.pdf
The Arduino code can be found in Arduino\Iridium9603Beacon
The Eagle files can be found in Eagle\V2
Version 2 of the PCB includes the following fixes:
- 1K pull-up resistors have been added to the I2C SCL and SDA lines
- C13 (0.1µF capacitor) is now 0603
- The 3V3 pin next to the SCL and SDA pins is now switched rather than always on

Did the GPS work correctly?
Sadly, no.
We flew two GlobalTop FGPMMOPA6H GPS modules to 35km on the SuperBIT flight: one worked correctly and one didn’t (it lost its fix and thought it was at 10,139m for most of the flight):


The two GPS modules were mounted on different parts of the balloon gondola, with different antennas and very different views of the sky. It was possible that the one that misbehaved simply wasn’t able to lock onto sufficient satellites during the flight and the failure was nothing to do with the module firmware.

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

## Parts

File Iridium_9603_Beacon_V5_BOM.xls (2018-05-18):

Part | X | Y | Angle | Package | Value | Manufacturer | Manufacturer Part No | Farnell Part No | Mouser Part No | McMaster Part No | Description | Alternative Part
Dimensions | 57.56 | 66.04
Fiducials - for solder paste mask alignment:
FD1 | 5.08 | 5.08 | 0 |  |  |  |  |  |  |  | Fiducial 1mm
FD2 | 49.94 | 60.96 | 0 |  |  |  |  |  |  |  | Fiducial 1mm
Surface Mount Components:
C1 | 30.48 | 23.91 | 180 | 0603 | 1uF | Walsin | 0603X105K100CT | 2496916 |  |  | MultiLayer Ceramic Capacitor; 1uF; 10V; 0603; X5R | 1uF 50V ±10% 0603 Samsung
C7 | 23.81 | 24.16 | 270 | 0603 | 1uF | Walsin | 0603X105K100CT | 2496916 |  |  | MultiLayer Ceramic Capacitor; 1uF; 10V; 0603; X5R | 1uF 50V ±10% 0603 Samsung
C14 | 38.86 | 31.59 | 0 | 0603 | 1uF | Walsin | 0603X105K100CT | 2496916 |  |  | MultiLayer Ceramic Capacitor; 1uF; 10V; 0603; X5R | 1uF 50V ±10% 0603 Samsung
C15 | 37.59 | 40.10 | 0 | 0603 | 1uF | Walsin | 0603X105K100CT | 2496916 |  |  | MultiLayer Ceramic Capacitor; 1uF; 10V; 0603; X5R | 1uF 50V ±10% 0603 Samsung
C2 | 40.96 | 26.45 | 0 | 0603 | 12pF | Walsin | 0603N120J500CT | 2496884 |  |  | MultiLayer Ceramic Capacitor; 12pF; 50V; 0603 | 12pF 50V ±5% 0603 Samsung
C4 | 40.96 | 28.92 | 0 | 0603 | 12pF | Walsin | 0603N120J500CT | 2496884 |  |  | MultiLayer Ceramic Capacitor; 12pF; 50V; 0603 | 12pF 50V ±5% 0603 Samsung
C3 | 16.26 | 35.21 | 270 | 0805 | 10uF | Walsin | 0805F106Z100CT | 2496998 |  |  | MultiLayer Ceramic Capacitor; 10uF; 10V; 0805 | 10uF 16V ±10% 0805 Samsung
C5 | 36.20 | 37.88 | 180 | 0805 | 10uF | Walsin | 0805F106Z100CT | 2496998 |  |  | MultiLayer Ceramic Capacitor; 10uF; 10V; 0805 | 10uF 16V ±10% 0805 Samsung
C6 | 18.16 | 27.30 | 0 | 0805 | 10uF | Walsin | 0805F106Z100CT | 2496998 |  |  | MultiLayer Ceramic Capacitor; 10uF; 10V; 0805 | 10uF 16V ±10% 0805 Samsung
C8 | 21.59 | 24.16 | 270 | 0805 | 10uF | Walsin | 0805F106Z100CT | 2496998 |  |  | MultiLayer Ceramic Capacitor; 10uF; 10V; 0805 | 10uF 16V ±10% 0805 Samsung
C10 | 19.05 | 44.48 | 0 | 0805 | 10uF | Walsin | 0805F106Z100CT | 2496998 |  |  | MultiLayer Ceramic Capacitor; 10uF; 10V; 0805 | 10uF 16V ±10% 0805 Samsung
C19 | 23.15 | 12.67 | 180 | 0805 | 10uF | Walsin | 0805F106Z100CT | 2496998 |  |  | MultiLayer Ceramic Capacitor; 10uF; 10V; 0805 | 10uF 16V ±10% 0805 Samsung
C9 | 15.24 | 38.13 | 0 | 0805 | 0.1uF | Walsin | 0805B104K500CT | 2496944 |  |  | MultiLayer Ceramic Capacitor; 0.1uF; 50V; 0805; X7R | 100nF 50V ±10% 0805 Samsung
C13 | 16.86 | 32.04 | 0 | 0805 | 0.1uF | Walsin | 0805B104K500CT | 2496944 |  |  | MultiLayer Ceramic Capacitor; 0.1uF; 50V; 0805; X7R | 100nF 50V ±10% 0805 Samsung
C16 | 36.77 | 46.70 | 0 | 0603 | 0.22uF | Multicomp | MC0603F224Z160CT | 1759019 |  |  | MultiLayer Ceramic Capacitor; 0.22uF; 16V; 0603 | 220nF 25V ±10% 0603 Samsung
C17 | 36.80 | 54.45 | 0 | 0805 | 2.2uF | Multicomp | MCTT21X225K100CT | 1759477 |  |  | MultiLayer Ceramic Capacitor; 2.2uF; 10V; 0805; X5R | 2.2uF 25V ±10% 0805 Samsung
C18 | 2.95 | 59.94 | 180 | 0805 | 10nF | Walsin | 0805B103K500CT | 2496939 |  |  | MultiLayer Ceramic Capacitor; 10nF; 50V; 0805; X7R | 10nF 50V ±5% 0805 Samsung
CON1 | 32.83 | 2.99 | 0 |  | Micro_USB | Amphenol_FCI | 10103594 | 2293752 |  |  | Amphenol FCI 10103594 Micro USB Type B | A01SB7X4X1B21-167 Micro USB 5S B
CON4 | 44.89 | 59.98 | 90 | uFL | uFL | Hirose | U.FL-R-SMT(01) | 3908021 |  |  | HIROSE U.FL-R-SMT(01); U.FL Coaxial; Straight Jack; 50 ohm
D1 | 20.99 | 50.58 | 180 | SOD-123 | MBR120 | ON SEMICONDUCTOR | MBR120VLSFT1G | 1431044 |  |  | Schottky Rectifier; 20V; 1A; SOD-123
D2 | 21.18 | 59.75 | 90 | SOD-123 | MBR120 | ON SEMICONDUCTOR | MBR120VLSFT1G | 1431044 |  |  | Schottky Rectifier; 20V; 1A; SOD-123
D3 | 38.23 | 59.79 | 90 | SOD-123 | MBR120 | ON SEMICONDUCTOR | MBR120VLSFT1G | 1431044 |  |  | Schottky Rectifier; 20V; 1A; SOD-123
D4 | 31.50 | 9.21 | 270 | SOD-123 | MBR120 | ON SEMICONDUCTOR | MBR120VLSFT1G | 1431044 |  |  | Schottky Rectifier; 20V; 1A; SOD-123
D5 | 52.67 | 56.86 | 90 | SOD-123 | MBR120 | ON SEMICONDUCTOR | MBR120VLSFT1G | 1431044 |  |  | Schottky Rectifier; 20V; 1A; SOD-123
D6 | 55.28 | 56.86 | 90 | SOD-123 | MBR120 | ON SEMICONDUCTOR | MBR120VLSFT1G | 1431044 |  |  | Schottky Rectifier; 20V; 1A; SOD-123
J1 | 26.27 | 42.10 | 0 |  | SS4-10-3.50 | Samtec | SS4-10-3.50-L-D-K-TR | 2085336 |  |  | Samtec SS4-10-3.50-L-D-K-TR
L1 | 11.78 | 59.98 | 0 | 0805 | 33nH | Coilcraft | 0805HT-33NTGLB | 2286465 |  |  | Surface Mount High Frequency Inductor; 0805; 33 nH; 600 mA | LQW2BHN33NJ03L Murata
LED1 | 25.05 | 8.83 | 0 |  | WS2812B | Sparkfun / Worldsemi | WS2812B |  | 474-COM-13667 |  | RGB LED with Driver
LED2 | 29.59 | 9.02 | 180 | 2.0x1.25 | RED | Wurth Electronik | 150080RS75000 | 2322077 | 710-150080RS75000 |  | LED; Red; 20mA; 2V; 2.0x1.25mm | Replaces Multicomp 703-0107
Q1 | 15.56 | 41.05 | 90 | SOT23 | DMG3415U-7 | Diodes Inc. | DMG3415U-7 | 1843688 |  |  | MOSFET; P Channel; SOT23-WIDE
Q2 | 18.48 | 56.86 | 0 | SOT23 | DMG3415U-7 | Diodes Inc. | DMG3415U-7 | 1843688 |  |  | MOSFET; P Channel; SOT23-WIDE
Q3 | 25.27 | 53.21 | 270 | SOT23 | DMG3415U-7 | Diodes Inc. | DMG3415U-7 | 1843688 |  |  | MOSFET; P Channel; SOT23-WIDE
Q4 | 32.89 | 41.69 | 0 | SOT23 | DMG3415U-7 | Diodes Inc. | DMG3415U-7 | 1843688 |  |  | MOSFET; P Channel; SOT23-WIDE
Q5 | 33.05 | 19.15 | 180 | SOT23 | 2N2222 | Fairchild | MMBT2222A | 9846700 |  |  | Bipolar (BJT) Single Transistor, NPN, 40 V, 350 mW, 1 A
R1 | 19.37 | 40.93 | 270 | 0805 | 100k | Multicomp | MC01W08051100K | 9332405 |  |  | Chip Resistor; Thick Film; 100k; 150V; 0805; 100mW | 100K ±1% 0805 RoyalOhm
R3 | 36.96 | 23.59 | 180 | 0805 | 100k | Multicomp | MC01W08051100K | 9332405 |  |  | Chip Resistor; Thick Film; 100k; 150V; 0805; 100mW | 100K ±1% 0805 RoyalOhm
R4 | 42.13 | 38.80 | 0 | 0805 | 100k | Multicomp | MC01W08051100K | 9332405 |  |  | Chip Resistor; Thick Film; 100k; 150V; 0805; 100mW | 100K ±1% 0805 RoyalOhm
R6 | 40.96 | 23.59 | 180 | 0805 | 100k | Multicomp | MC01W08051100K | 9332405 |  |  | Chip Resistor; Thick Film; 100k; 150V; 0805; 100mW | 100K ±1% 0805 RoyalOhm
R12 | 18.48 | 54.01 | 0 | 0805 | 100k | Multicomp | MC01W08051100K | 9332405 |  |  | Chip Resistor; Thick Film; 100k; 150V; 0805; 100mW | 100K ±1% 0805 RoyalOhm
R13 | 21.88 | 53.21 | 270 | 0805 | 100k | Multicomp | MC01W08051100K | 9332405 |  |  | Chip Resistor; Thick Film; 100k; 150V; 0805; 100mW | 100K ±1% 0805 RoyalOhm
R2 | 48.32 | 46.86 | 0 | 0805 | 12K | Panasonic | ERJ6ENF1202V | 2303661 |  |  | Chip Resistor; Thick Film; 12k; 150V; 0805; 125mW | 12K ±1% 0805 RoyalOhm
R5 | 16.95 | 29.85 | 0 | 0603 | 1K | Multicomp | MCWR06X1001FTL | 2447272 |  |  | Chip Resistor; Thick Film; 1k; 50V; 0603; 100mW | 1K ±1% 0603 RoyalOhm
R8 | 12.76 | 29.85 | 180 | 0603 | 1K | Multicomp | MCWR06X1001FTL | 2447272 |  |  | Chip Resistor; Thick Film; 1k; 50V; 0603; 100mW | 1K ±1% 0603 RoyalOhm
R10 | 29.56 | 12.35 | 270 | 0603 | 1K | Multicomp | MCWR06X1001FTL | 2447272 |  |  | Chip Resistor; Thick Film; 1k; 50V; 0603; 100mW | 1K ±1% 0603 RoyalOhm
R14 | 34.42 | 23.18 | 270 | 0603 | 1K | Multicomp | MCWR06X1001FTL | 2447272 |  |  | Chip Resistor; Thick Film; 1k; 50V; 0603; 100mW | 1K ±1% 0603 RoyalOhm
R7 | 35.37 | 13.72 | 0 | 0603 | 47k | Multicomp | MCWR06X4702FTL | 2447376 |  |  | Chip Resistor; Thick Film; 47k; 50V; 0603; 100mW | 47K ±1% 0603 RoyalOhm
R9 | 8.00 | 59.98 | 180 | 0805 | 10 ohm | Multicomp | MC01W0805110R | 9332421 |  |  | Chip Resistor; Thick Film; 10 ohm; 150V; 0805; 100mW | 10R ±1% 0805 RoyalOhm
R11 | 53.40 | 46.86 | 180 | 0805 | 30K | Panasonic | ERJ6GEYJ303V | 2323830 |  |  | Chip Resistor; Thick Film; 30k; 150V; 0805; 125 mW | 30K ±1% 0805 RoyalOhm
R15 | 32.83 | 39.18 | 180 | 0603 | 10K | Multicomp | MCWR06X1002FTL | 2447230 |  |  | Chip Resistor; Thick Film; 10k; 50V; 0603; 100mW | 10K ±1% 0603 RoyalOhm
R16 | 42.26 | 40.80 | 0 | 0603 | 10K | Multicomp | MCWR06X1002FTL | 2447230 |  |  | Chip Resistor; Thick Film; 10k; 50V; 0603; 100mW | 10K ±1% 0603 RoyalOhm
R17 | 32.83 | 23.18 | 270 | 0603 | 10K | Multicomp | MCWR06X1002FTL | 2447230 |  |  | Chip Resistor; Thick Film; 10k; 50V; 0603; 100mW | 10K ±1% 0603 RoyalOhm
SW1 | 24.13 | 3.18 | 180 | 4.6x2.8 | Tactile Switch | Multicomp | MCIPTG23K-V | 1605470 |  |  | Tactile Switch; 4.6x2.8mm; 50mA; 12V
U1 | 29.69 | 20.22 | 0 | SOT23-3 | MCP111T-240E/TT | Microchip | MCP111T-240E/TT | 1627192 |  |  | Reset Supervisor; SOT23-3; 2.40V; Open Drain; Active Low
U2 | 17.78 | 24.16 | 270 | SOT23-5 | SPX3819-3.3 | Exar | SPX3819M5-L-3-3/TR |  | 701-SPX3819M5-L-33TR |  | LDO Voltage Regulator; 500mA; SOT-23-5
U3 | 39.05 | 43.02 | 90 | DFN-10 | LTC3225EDDB | Linear Technology | LTC3225EDDB#TRMPBF | 1715231 |  |  | Supercapacitor Charger
U4 | 12.03 | 33.69 | 180 | LGA8 | MPL3115A2 | NXP | MPL3115A2 | 2009084 |  |  | Pressure Sensor
U5 | 30.48 | 30.26 | 90 | TQFN48 | ATSAMD21G18A | Atmel | ATSAMD21G18A-MF | 2460544 |  |  | ATSAMD21G18A-MF; QFN48
U6 | 9.41 | 52.63 | 270 |  | MAX-M8Q | u-blox | MAX-M8Q |  |  |  | https://www.u-blox.com/en/product/max-m8-series
U7 | 35.46 | 9.75 | 0 | MSOP8 | LT1634BCMS8-1.25 | Linear Technology | LT1634BCMS8-1.25 | 2252797 | 584-1634BCMS8-1.25PF |  | 1.25V Precision Voltage Reference
X1 | 37.66 | 27.72 | 270 | 3.2x1.5 | 32.768 | Epson | Q13FC13500004 | 1278036 |  |  | Crystal; 32.768kHz; 12.5pF; 3.2 x 1.5mm
Press-In Nuts for Iridium 9603N:
S1 | 16.27 | 16.50 |  |  | Press-In Nut | McMaster-Carr | 95117A411 |  |  | 95117A411 | Press-In Nut; 2-56
S2 | 41.27 | 16.50 |  |  | Press-In Nut | McMaster-Carr | 95117A411 |  |  | 95117A411 | Press-In Nut; 2-56
Non-surface mount components:
BAT1 |  |  |  |  | AA-Clip_Pair | Keystone Electronics | 92 | 908733 |  |  | Keystone Electronics 92 AA Battery Clip (Pair)
BAT2 |  |  |  |  | AA-Clip_Pair | Keystone Electronics | 92 | 908733 |  |  | Keystone Electronics 92 AA Battery Clip (Pair)
BAT3 |  |  |  |  | AA-Clip_Pair | Keystone Electronics | 92 | 908733 |  |  | Keystone Electronics 92 AA Battery Clip (Pair)
C11 |  |  |  |  | 1F 2.7V | Bussmann | HV0810-2R7105-R | 2148482 |  |  | Supercapacitor; 1F; 2.7V; +30%, -10%; 3.5mm Pitch
C12 |  |  |  |  | 1F 2.7V | Bussmann | HV0810-2R7105-R | 2148482 |  |  | Supercapacitor; 1F; 2.7V; +30%, -10%; 3.5mm Pitch
CON2 |  |  |  |  | SMA Jack | Johnson | 142-0711-821 | 1019328 |  |  | SMA End Launch Jack
CON3 |  |  |  |  | SMA Jack | Johnson | 142-0711-821 | 1019328 |  |  | SMA End Launch Jack
RELAY1 |  |  |  |  | DPDT Latching | Omron | G6SK-2 3VDC |  | 653-G6SK-2DC3 |  | DPDT Latching Relay (Dual Coil) 3VDC
Iridium 9603N:
9603N |  |  |  |  |  | Iridium | 9603N |  |  |  | https://www.iridium.com/products/iridium-9603/
Mounting hardware for Iridium 9603N:
SPACERS_x2 |  |  |  |  |  |  |  |  |  | 94669A100 | 4.5mm OD x 6mm Spacers for Iridium Module
SCREWS_x2 |  |  |  |  |  |  |  |  |  | 92185A081 | 2-56 x 7/16 Screws for Iridium Module
Cable for Iridium 9603N:
CABLE |  |  |  |  |  | HIROSE (HRS) | U.FL-2LP-088K1T-A-50 | 1688071 |  |  | HIROSE u.FL - u.FL cable 50ohm 50mm
SMA Antennas:
Iridium |  |  |  |  |  | Maxtena | M1621HCT-SMA | 2281619 |  |  | Iridium Passive Antenna with SMA connector
GNSS |  |  |  |  |  | Maxtena | M1516HCT-P-SMA | 2484960 |  |  | GPS / Glonass Passive Antenna with SMA connector
For solar operation:
Don't install BAT1-BAT3 battery clips
Replace C11 and C12 with 10F capacitors. Install these flat against the underside of the PCB, carefully bending the legs to fit.
C11 & C12 |  |  |  |  | 10F 2.7V | Bussmann | HV1030-2R7106-R | 2148486 |  |  | Supercapacitor; 10F; 2.7V; +30%, -10%; 5.0mm Pitch
Connect two PowerFilm MPT3.6-150 solar panels to the SOLAR+/- terminals. Be careful with the panel polarity.
Set the supercapacitor charge current to 60mA via the split pads. Carefully cut the track between the 150mA pads and solder across the 60mA pads.

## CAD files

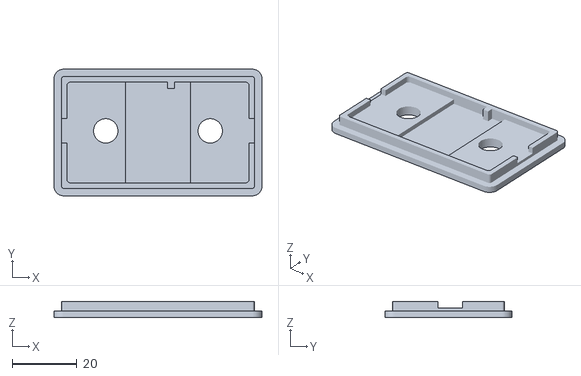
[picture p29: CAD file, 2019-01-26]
OpenSCAD/With_Radio_Board/Lid_With_Radio.stl
64.0 x 39.0 x 5.00

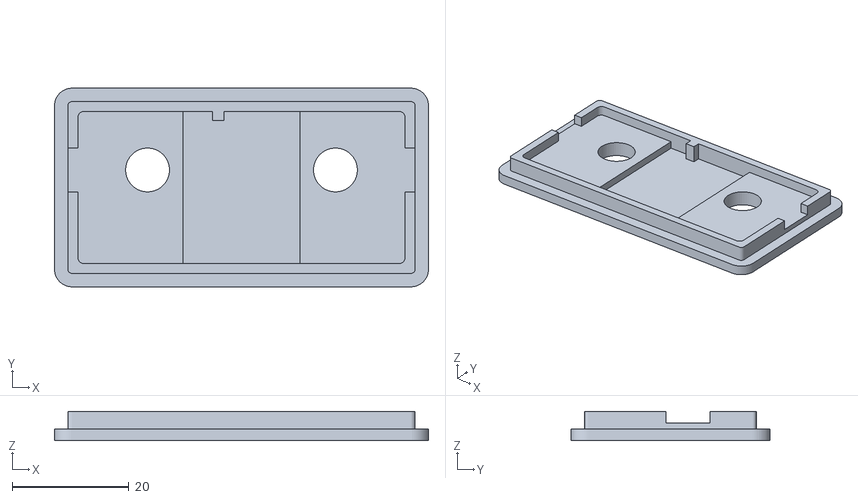
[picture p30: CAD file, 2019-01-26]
OpenSCAD/Without_Radio_Board/Lid_Without_Radio.stl
64.0 x 34.0 x 5.00

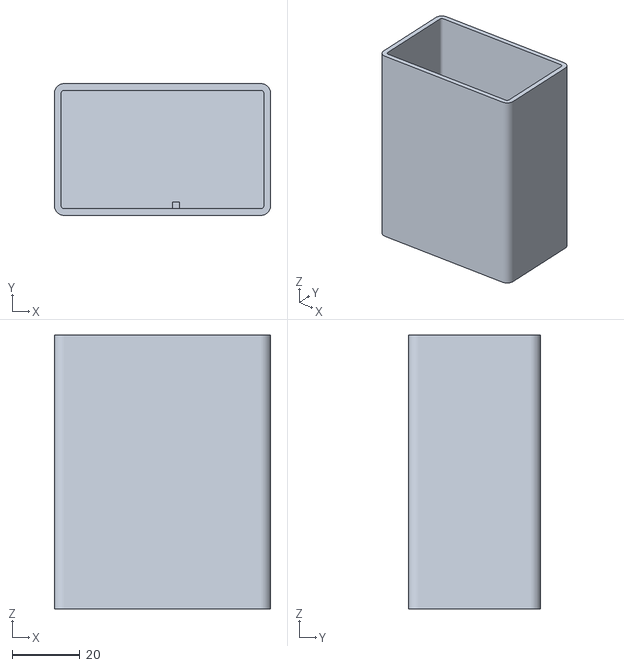
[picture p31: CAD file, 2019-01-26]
OpenSCAD/With_Radio_Board/Cover_With_Radio.stl
64.0 x 39.0 x 81.0

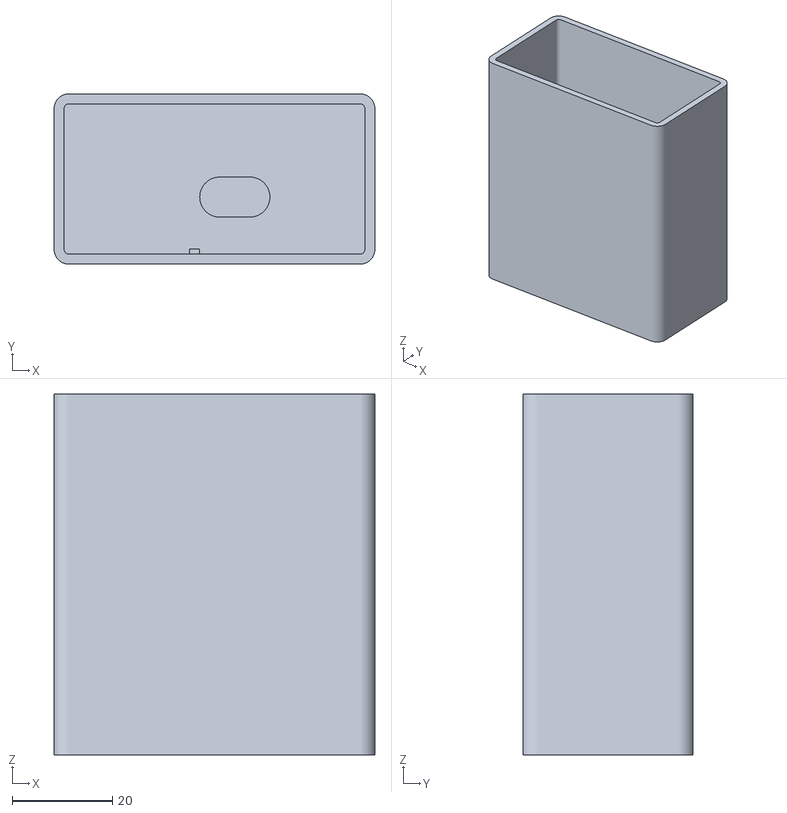
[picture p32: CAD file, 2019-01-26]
OpenSCAD/Without_Radio_Board/Cover_Without_USB.stl
64.0 x 34.0 x 72.0

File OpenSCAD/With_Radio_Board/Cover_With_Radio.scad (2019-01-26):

// Simple Cover for the Iridium Beacon with Radio Board

$fn=50; // fragments
wall = 2.0; // wall thickness
internal_width = 60.0; // internal width (X) of the cover
internal_depth = 35.0; // internal depth (Y) of the cover
internal_height = 78.0; // internal height (Z) of the cover
lid_insert = 1.0; // extra height for the lid insert

internal_corner_radius = 1.0; // radius of the internal corner cylinder

support_x_offset = 4.0; // x offset of the support w.r.t. the X center of the void
support_width = 2.0; // x width of the support
support_depth = 2.0; // y depth of the support
support_height = 55.0; // z height of the support

height = internal_height + wall + lid_insert; // cover external height (Z)
width = internal_width + (2 * wall); // cover external width (X)
depth = internal_depth + (2 * wall); // cover external depth (Y)

external_corner_radius = internal_corner_radius + wall; // external corner radius

module cover()
{
    translate([external_corner_radius, external_corner_radius, 0])
        minkowski() {
            cube([(width - (2 * external_corner_radius)), (depth - (2 * external_corner_radius)), (height / 2)]);
            cylinder(h=(height / 2), r=external_corner_radius);
        }
}

module void()
// Void will be higher than required to avoid zero thickness skin across opening
{
    translate([external_corner_radius, external_corner_radius, wall])
        minkowski() {
            cube([(internal_width - (2 * internal_corner_radius)), (internal_depth - (2 * internal_corner_radius)), (height / 2)]);
            cylinder(h=(height / 2), r=internal_corner_radius);
        }
}

module support()
{
    translate([((width / 2) + support_x_offset - (support_width / 2)),wall, 0]) {
        cube([support_width, support_depth, (support_height + wall)]);
    }
}

module finished_cover()
{
    union() {
        difference() {
            cover();
            void();
        }
        support();
    }
}

finished_cover();

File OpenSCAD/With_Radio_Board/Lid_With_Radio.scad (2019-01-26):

// Simple Lid for the Iridium Beacon Cover with Radio Board

$fn=50; // fragments
wall = 2; // cover wall thickness
thickness = 2; // lid end thickness
internal_width = 60; // internal width (X) of the cover
internal_depth = 35; // internal depth (Y) of the cover
gap = 0.3; // clearance gap (per side)
insert_height = 3; // extra height for the lid insert
internal_corner_radius = 1.0; // radius of the internal corner cylinder

sma_r = 3.75; // radius of the hole for the sma connector
sma_x_sep = 1.266 * 25.4; // X separation of the two SMA connectors
sma_y_offset = 0.5; // y offset of the holes for the sma connectors w.r.t. the Y center of the void
sma_wall_thickness = 3.0; // wall thickness around the SMA connectors

relay_recess_width = 20.0; // width of the recess for the relay terminals
relay_wall_thickness = 1.5; // wall thickness across the relay recess

support_x_offset = 4.0; // x offset of the support w.r.t. the X center of the void
support_width = 2.0; // x width of the support
support_depth = 2.0; // y depth of the support

if (gap > internal_corner_radius) echo("Error! Gap cannot be greater than the internal corner radius!");

width = internal_width + (2 * wall); // lid external width (X)
depth = internal_depth + (2 * wall); // lid external depth (Y)

total_height = wall + insert_height; // total height of the lid

sma_1_x = (width / 2) - (sma_x_sep / 2); // x position of sma connector 1
sma_2_x = (width / 2) + (sma_x_sep / 2); // x position of sma connector 2
sma_y = (depth / 2) + sma_y_offset; // y position of the sma connectors

external_corner_radius = internal_corner_radius + wall; // external corner radius

module outer()
{
    translate([external_corner_radius, external_corner_radius, 0])
        minkowski() {
            cube([(width - (2 * external_corner_radius)), (depth - (2 * external_corner_radius)), (thickness / 2)]);
            cylinder(h=(thickness / 2), r=external_corner_radius);
        }
}

module inner()
// Thicker than required to avoid zero thickness joints
{
    translate([external_corner_radius, external_corner_radius, 0])
        minkowski() {
            cube([(width - (2 * external_corner_radius)), (depth - (2 * external_corner_radius)), (total_height / 2)]);
            cylinder(h=(total_height / 2), r=(internal_corner_radius - gap));
        }
}

module recess()
// Thicker than required to avoid zero thickness joints
{
    translate([(internal_corner_radius + wall + wall), (internal_corner_radius + wall + wall), sma_wall_thickness])
        minkowski() {
            cube([(width - (2 * (wall + wall + internal_corner_radius))), (depth - (2 * (wall + wall + internal_corner_radius))), (total_height / 2)]);
            cylinder(h=(total_height / 2), r=internal_corner_radius);
        }
}

module lid()
{
    union() {
        outer();
        inner();
    }
}

module sma_1()
// Cylinder is taller than required to avoid zero thickness skins
{
    translate([sma_1_x, sma_y, -1]) {
        cylinder(h=(total_height + 2),r=sma_r);
    }
}

module sma_2()
// Cylinder is taller than required to avoid zero thickness skins
{
    translate([sma_2_x, sma_y, -1]) {
        cylinder(h=(total_height + 2),r=sma_r);
    }
}

module pcb_slot()
// Cube is taller amd wider than required to avoid zero thickness skins
{
    translate([0, (sma_y - sma_r), sma_wall_thickness]) {
        cube([width, (sma_r * 2), total_height]);
    }
}

module relay_recess()
// Recess is higher than required to avoid zero thickness skins
{
    translate([((width / 2) - (relay_recess_width / 2)), (2 * wall), relay_wall_thickness]) {
        cube([relay_recess_width, (depth - (4 * wall)), total_height]);
    }
}

module support()
{
    translate([((width / 2) + support_x_offset - (support_width / 2)),(depth - ((2 * wall) + support_depth)), 0]) {
        cube([support_width, support_depth, total_height]);
    }
}

module finished_lid()
{
    union() {
        difference() {
            lid();
            sma_1();
            sma_2();
            recess();
            pcb_slot();
            relay_recess();
        }
        support();
    }
}

finished_lid();

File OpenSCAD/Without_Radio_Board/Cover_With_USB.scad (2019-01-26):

// Simple Cover for the Iridium Beacon with USB opening

$fn=50; // fragments
wall = 2.0; // wall thickness
end_wall = 3.0; // end wall thickness
internal_width = 60.0; // internal width (X) of the cover
internal_depth = 30.0; // internal depth (Y) of the cover
internal_height = 68.5; // internal height (Z) of the cover
lid_insert = 1.0; // extra height for the lid insert

internal_corner_radius = 1.0; // radius of the internal corner cylinder

support_x_offset = -4.0; // x offset of the support w.r.t. the X center of the void
support_width = 2.0; // x width of the support
support_depth = 1.5; // y depth of the support
support_height = 55.0; // z height of the support

usb_r = 2.0; // radius of the opening for the USB connector
usb_width = 10.0; // total width of the opening for the USB
usb_height = 1.0; // thickness of the opening for the USB connector
usb_recess_r = 4.0; // radius of the recess for the USB connector body
usb_recess_width = 12.0; // total width of the recess for the USB connector body
usb_x_offset = 4.05; // X offset of the USB connector
usb_y_offset = 3.6; // y offset of the USB connector

height = internal_height + end_wall + lid_insert; // cover external height (Z)
width = internal_width + (2 * wall); // cover external width (X)
depth = internal_depth + (2 * wall); // cover external depth (Y)

external_corner_radius = internal_corner_radius + wall; // external corner radius

module cover()
{
    translate([external_corner_radius, external_corner_radius, 0])
        minkowski() {
            cube([(width - (2 * external_corner_radius)), (depth - (2 * external_corner_radius)), (height / 2)]);
            cylinder(h=(height / 2), r=external_corner_radius);
        }
}

module void()
// Void will be higher than required to avoid zero thickness skin across opening
{
    translate([external_corner_radius, external_corner_radius, end_wall])
        minkowski() {
            cube([(internal_width - (2 * internal_corner_radius)), (internal_depth - (2 * internal_corner_radius)), (height / 2)]);
            cylinder(h=(height / 2), r=internal_corner_radius);
        }
}

module usb_opening_end_1()
// Cylinder is taller than it needs to be to avoid zero thickness skins
{
    translate([((usb_width / 2) - usb_r),0,usb_height]) {
        cylinder(h=end_wall,r=usb_r);
    }
}

module usb_opening_end_2()
// Cylinder is taller than it needs to be to avoid zero thickness skins
{
    translate([(0-((usb_width / 2) - usb_r)),0,usb_height]) {
        cylinder(h=end_wall,r=usb_r);
    }
}

module usb_opening_mid()
// Cube is taller than it needs to be to avoid zero thickness skins
{
    translate([(-0.5 * (usb_width - (2 * usb_r))), (-0.5 * (2 * usb_r)), usb_height]) {
        cube([(usb_width - (2 * usb_r)), (2 * usb_r), end_wall]);
    }
}

module usb_recess_end_1()
// Cylinder is taller than it needs to be to avoid zero thickness skins
{
    translate([((usb_recess_width / 2) - usb_recess_r), 0, (0 - usb_height)]) {
        cylinder(h=end_wall, r=usb_recess_r);
    }
}

module usb_recess_end_2()
// Cylinder is taller than it needs to be to avoid zero thickness skins
{
    translate([(0-((usb_recess_width / 2) - usb_recess_r)), 0, (0 - usb_height)]) {
        cylinder(h=end_wall, r=usb_recess_r);
    }
}

module usb_recess_mid()
// Cube is taller than it needs to be to avoid zero thickness skins
{
    translate([(-0.5 * (usb_recess_width - (2 * usb_recess_r))), (-0.5 * (2 * usb_recess_r)), (0 - usb_height)]) {
        cube([(usb_recess_width - (2 * usb_recess_r)), (2 * usb_recess_r), end_wall]);
    }
}

module usb()
{
    translate([((width / 2) + usb_x_offset), ((depth / 2) - usb_y_offset), 0]) {
        union() {
            usb_opening_end_1();
            usb_opening_end_2();
            usb_opening_mid();
            usb_recess_end_1();
            usb_recess_end_2();
            usb_recess_mid();
        }
    }
}

module support()
{
    translate([((width / 2) + support_x_offset - (support_width / 2)),wall, 0]) {
        cube([support_width, support_depth, (support_height + end_wall)]);
    }
}

module finished_cover()
{
    union() {
        difference() {
            cover();
            void();
            usb();
        }
        support();
    }
}

finished_cover();

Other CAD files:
OpenSCAD/Without_Radio_Board/Cover_With_USB.stl
OpenSCAD/Without_Radio_Board/Cover_Without_USB.scad
OpenSCAD/Without_Radio_Board/Lid_Without_Radio.scad

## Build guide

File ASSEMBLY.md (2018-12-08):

# Iridium 9603N Beacon Assembly Instructions

Here are the assembly instructions for V5 of the Iridium 9603N Beacon:

### Blank PCB

Start by having the blank PCBs manufactured. If you are based in the UK or Europe, I can recommend
[Multi-CB](https://www.multi-circuit-boards.eu/en/index.html) who can manufacture PCBs in 1-8 working days and
can process the Eagle .brd file direct - there's no need to generate Gerber files.

My recommended options are:
- Layers: 2 layers
- Format: single pieces
- Surface finish: chemical gold (ENIG)
- Material: FR4, 1.55mm
- Cu layers: 35um
- Solder stop: both sides, green
- Marking print: both sides, white

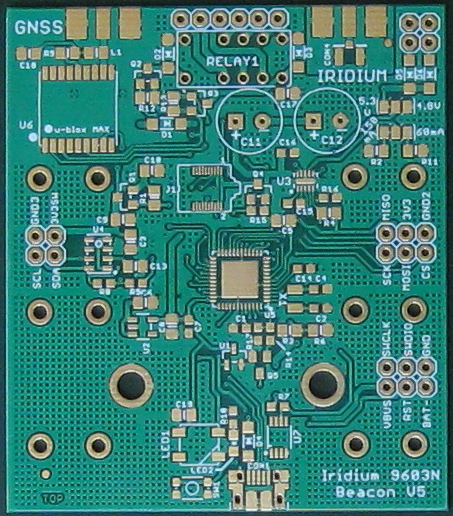
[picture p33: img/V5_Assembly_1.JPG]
V5_Assembly_1


### Add solder paste

Multi-CB can also provide you with a solder paste (SMD) stencil for the PCB. My recommended options are:
- SMD stencil for: top layer
- Make the Y dimension 20mm longer than the PCB itself to allow you to fix it down with tape
- Type: custom
- Pad reduction: yes, 10%
- Thickness: 100um
- Existing fiducials: lasered through
- Text type: half lasered
- Double-sided brushing: yes

The solder paste stencil will - by default - have tCream cut-outs for _all_ of the surface mount components.
If you intend to solder some of the components by hand, you can if you wish provide a separate stencil design
containing cut-outs for only the 'tricky' components: J1 and U3 in particular.

I secure the blank PCB onto a flat work surface by locating it between two engineer's squares. I use a sheet of toughened glass
as the work surface as it is both very flat and easy to clean.

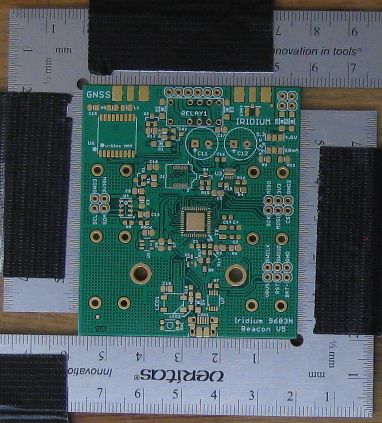
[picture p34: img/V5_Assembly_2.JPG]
V5_Assembly_2


Use the two round fiducials to line up the stencil with the PCB. Secure the stencil with tape.

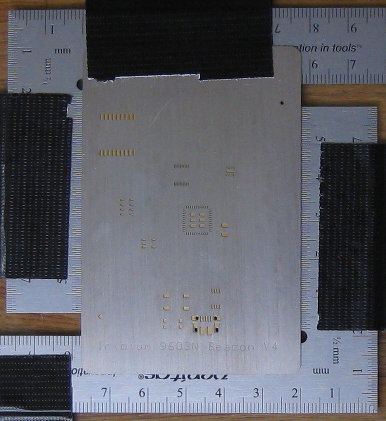
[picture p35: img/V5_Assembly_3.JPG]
V5_Assembly_3


Apply solder paste close to the component cut-outs and then scrape the paste over the stencil using a knife blade
or a similar straight edge. Take appropriate safety precautions when working with solder paste - particularly if you are using
tin-lead solder instead of lead-free.

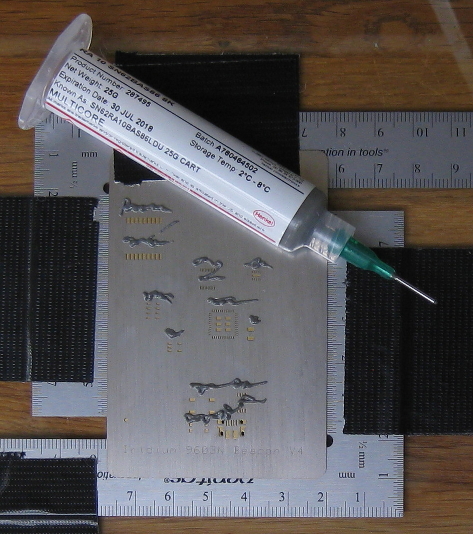
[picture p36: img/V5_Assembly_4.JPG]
V5_Assembly_4


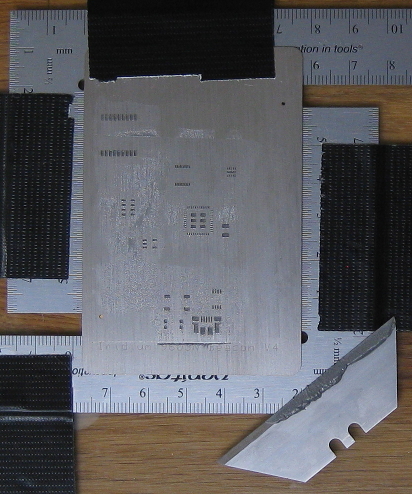
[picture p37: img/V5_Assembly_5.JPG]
V5_Assembly_5


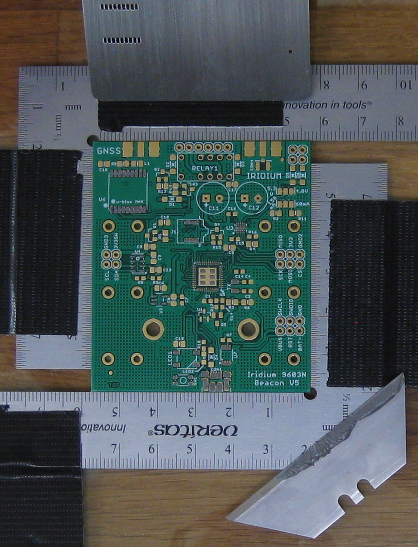
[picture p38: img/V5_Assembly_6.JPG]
V5_Assembly_6


### Position the surface mount components

Position the components onto the blobs of solder paste using tweezers. A magnifier lamp or a USB microscope will
help you place the components in the correct position. J1 - the 20-way Samtec connector - is probably the trickiest
component to position. Take extra time to make sure the legs are centered accurately on the pads.

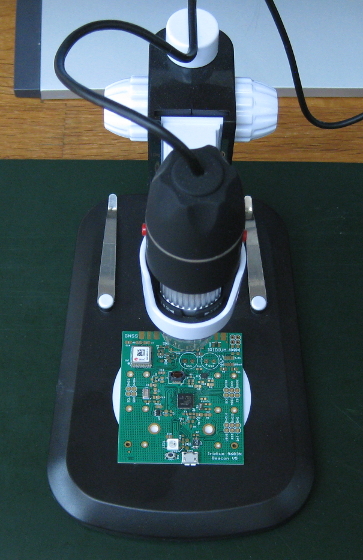
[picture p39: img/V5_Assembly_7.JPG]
V5_Assembly_7


### Reflow the surface mount components

Use a reflow oven to heat the circuit board to the correct temperatures to melt the solder. A reflow oven doesn't need to be
expensive. The one shown below was assembled from:

- Quest 9L 800W mini-oven
- Inkbird PID temperature controller and 40A solid state relay
- Type K thermocouple

Several people have published good reflow oven construction guides, including [this one](http://www.die4laser.com/toaster/index.html).

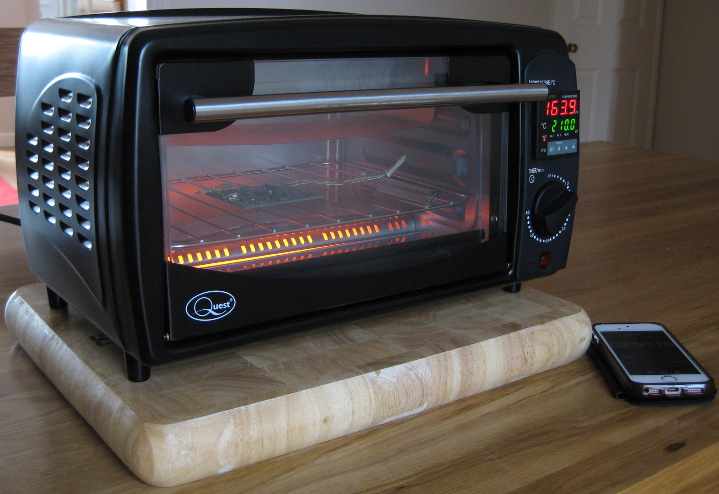
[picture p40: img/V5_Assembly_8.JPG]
V5_Assembly_8


Use the correct temperature profile for your solder paste, but you won't go far wrong with 160C for four minutes, followed by
210C for one minute, followed by a cool-down with the door open. Use a flashlight to check that the solder has melted across
the whole PCB at 210C. Hold the temperature at 210C a little longer if some of the solder paste still appears 'gray' instead of 'silver'.

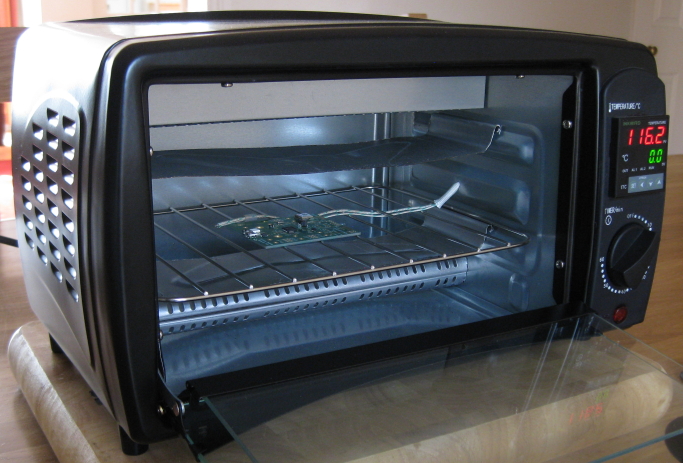
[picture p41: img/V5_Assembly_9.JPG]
V5_Assembly_9


### Check for shorts

Carefully examine all the solder joints and correct any shorts you find.

The 'trick' to removing a short is to add more solder or solder paste and then to use
copper solder braid or wick to remove all the solder in one go.

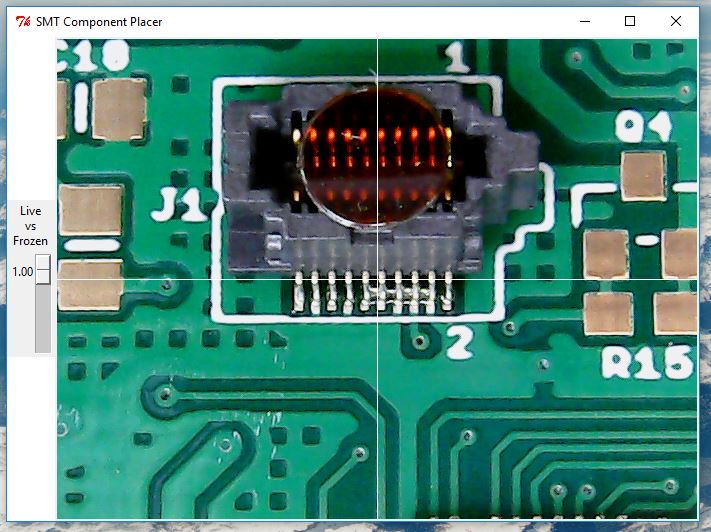
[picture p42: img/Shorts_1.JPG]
Shorts_1


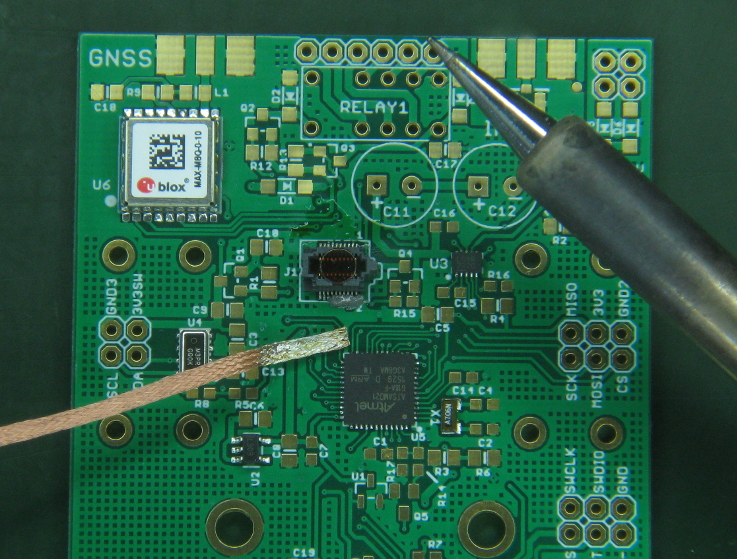
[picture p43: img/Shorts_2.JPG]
Shorts_2


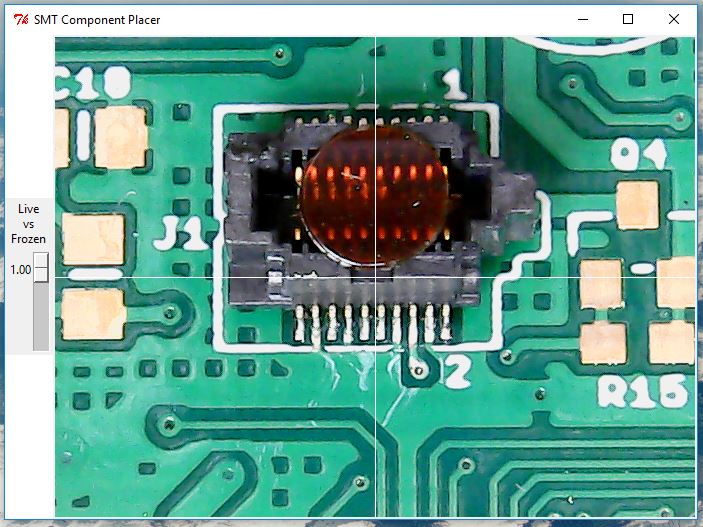
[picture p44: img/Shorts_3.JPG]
Shorts_3


Solder any remaining surface mount components by hand and then use a cotton bud (q-tip) dipped in Iso-Propyl Alcohol
(IPA / Propanol / rubbing alcohol) to remove any flux residue.

All being well, your PCB should look like this:

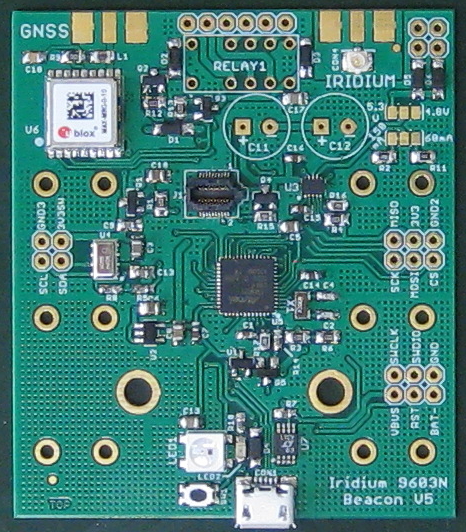
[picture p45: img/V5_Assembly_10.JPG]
V5_Assembly_10


### Press-in nuts

The Iridium 9603N module is held in place by two 2-56 screws. The threaded 2-56 press-in nuts now need to be pressed into the rear of the
PCB. These are McMaster part number 95117A411. The nuts are best pressed into place using an arbor press, but the corners of the circuit
board have been deliberately kept clear of components so you can press the nuts in using a standard workshop vice if required.

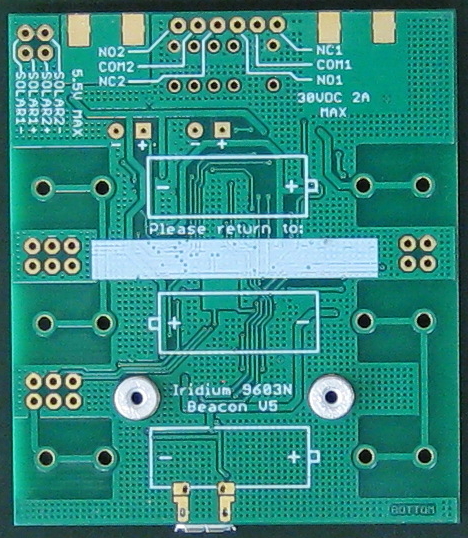
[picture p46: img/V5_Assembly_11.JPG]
V5_Assembly_11


### Add the non-surface mount components

The non-surface mount components (battery clips, relay, super capacitors, SMA conectors) can now be soldered in by hand. If you are
going to be using solar power, omit the battery clips and use 10F super capacitors instead of 1F. See
[Power Options](https://github.com/PaulZC/Iridium_9603_Beacon/blob/master/LEARN.md#power-options) for further details.

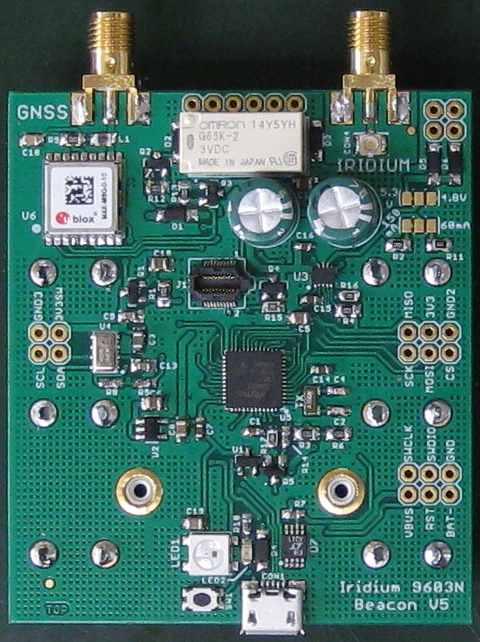
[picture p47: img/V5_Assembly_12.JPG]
V5_Assembly_12


V5_Assembly_13

### Install the bootloader

The SAMD21G18A processor now needs to be configured with a bootloader using a J-Link programmer or similar. See
[How do I install the ATSAMD21G18 Bootloader](https://github.com/PaulZC/Iridium_9603_Beacon/blob/master/LEARN.md#how-do-i-install-the-atsamd21g18-bootloader)
for further details.

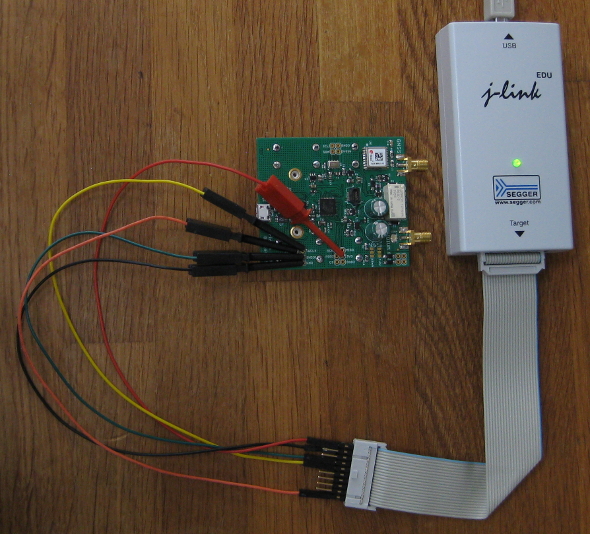
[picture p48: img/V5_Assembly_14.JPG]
V5_Assembly_14


### Test the PCB

Before connecting the Iridium 9603N, it is a good idea to test the completed PCB. The [Arduino](https://github.com/PaulZC/Iridium_9603_Beacon/tree/master/Arduino)
directory contains a sketch called Iridium_9603N_Beacon_V5_Test which will test all of the components on the PCB for you. Messages are displayed
on the Arduino IDE Serial Monitor as each test is passed.

### Install the Iridium 9603N module

Take appropriate ESD precautions throughout and especially when handling the 9603N module.

Connect the 9603N to the beacon PCB using a HIROSE (HRS) u.FL-u.FL cable or similar. The cable needs to be 50 Ohm and approximately 50mm long.

V5_Assembly_15

Carefully fold the 9603N module over onto the PCB, insert the 20-way connector into the Samtec socket, then secure the module using:
- two 4.5mm OD x 6mm spacers (McMaster 94669A100)
- two 2-56 x 7/16" screws (McMaster 92185A081)

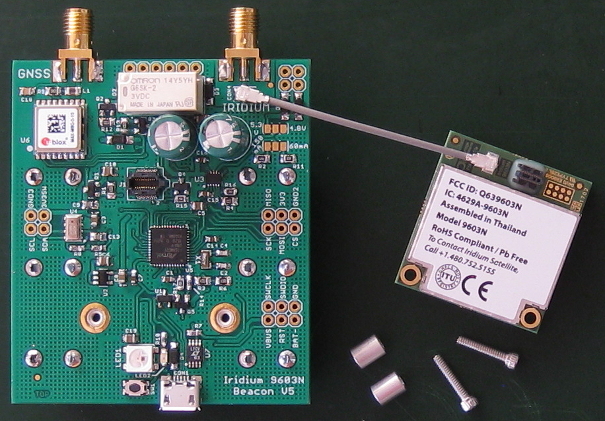
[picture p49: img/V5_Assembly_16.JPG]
V5_Assembly_16


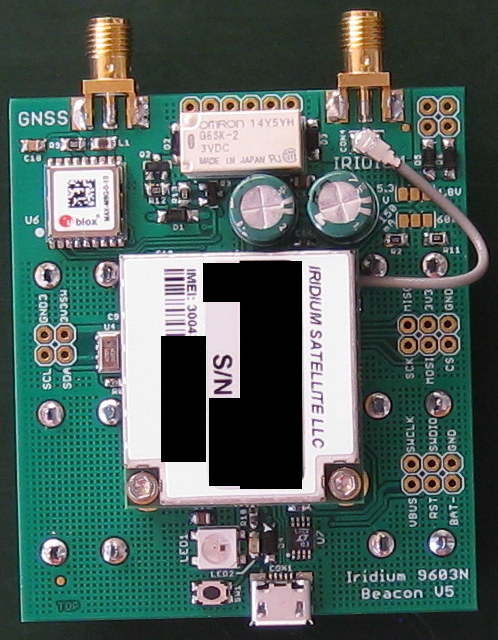
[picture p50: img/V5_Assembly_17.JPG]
V5_Assembly_17


Screw the GNSS and Iridium antennas onto the SMA connectors

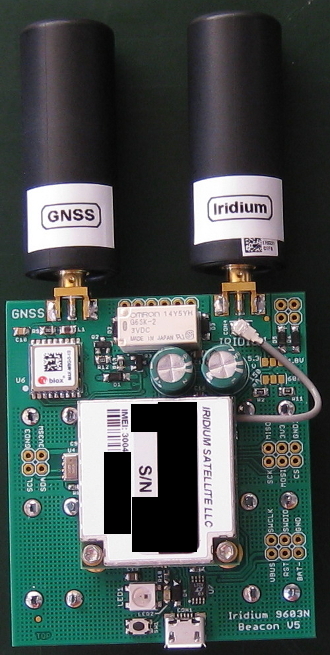
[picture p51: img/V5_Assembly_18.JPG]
V5_Assembly_18


### Retest the PCB

Now that the 9603N has been installed, retest the completed PCB using the [Arduino test code](https://github.com/PaulZC/Iridium_9603_Beacon/tree/master/Arduino).

### Secure J1 with Epoxy

I recommend securing J1 to the PCB with a small amount of epoxy to make it more robust. 3M Scotch-Weld 2216 is an ideal choice as it remains slightly flexible when cured.
You will need to temporarily remove the 9603N while you apply the epoxy. Apply the mixed epoxy around the body and legs of J1 using a toothpick,
taking great care to keep the epoxy clear of the connector opening and pins. Make sure the epoxy is fully cured before re-installing the 9603N.

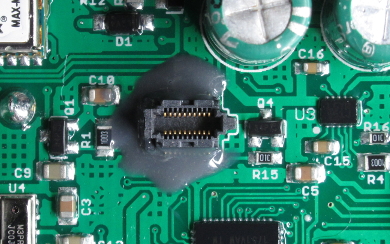
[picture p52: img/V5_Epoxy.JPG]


### Lacquer the PCB

I recommend giving the PCB a coat of lacquer, especially if you are intending to use it to track a balloon flight.
You will need to temporarily remove the 9603N while you apply the lacquer. Cover all of the surface mount components with
[Acrylic Protective Lacquer (conformal coating)](https://uk.rs-online.com/web/p/conformal-coatings/3217324/) except: U4 (pressure sensor), J1, SW1, CON1, IO pads and split pads.

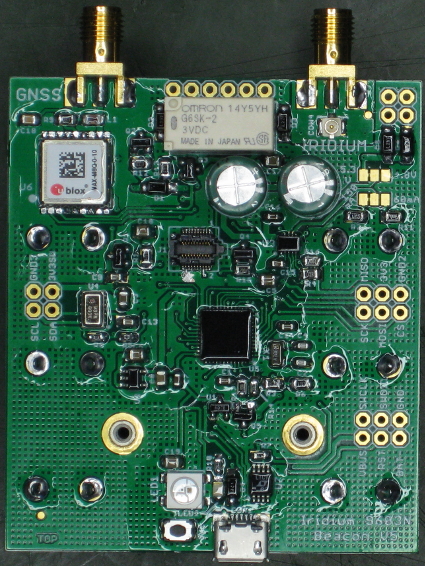
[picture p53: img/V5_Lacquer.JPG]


### Ready to fly!

Insert three Energiser® Ultimate Lithium AA batteries into the battery clips

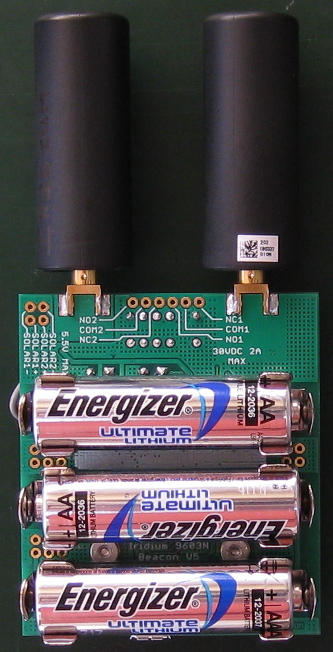
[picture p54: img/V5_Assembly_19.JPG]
V5_Assembly_19


The completed beacon is an almost perfect fit in a [Peli 1015 Micro Case](https://peliproducts.co.uk/1015-micro-case.html)
(The 1015 case is also available in Clear&Yellow or Clear&Black)

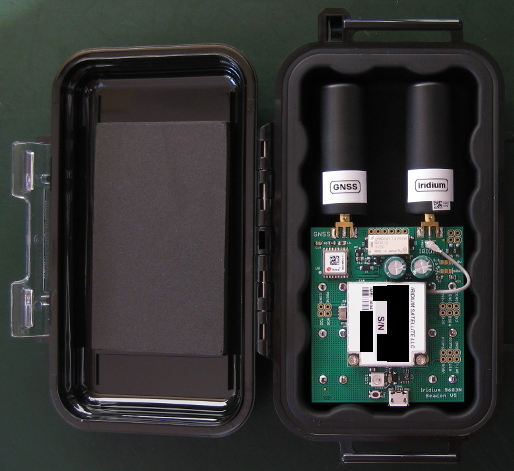
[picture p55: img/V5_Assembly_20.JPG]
V5_Assembly_20


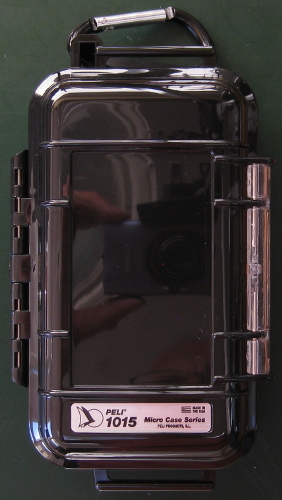
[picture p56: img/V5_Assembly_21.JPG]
V5_Assembly_21


### The Small Print

This project is distributed under a Creative Commons Attribution + Share-alike (BY-SA) licence.
Please refer to section 5 of the licence for the "Disclaimer of Warranties and Limitation of Liability".

Enjoy!

**_Paul_**

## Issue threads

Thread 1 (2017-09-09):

Best way to set up data service with Iridium ...

dwblair, 2017-09-09:
Hi Paul!

Fantastic, inspiring project.  We're looking to deploy some environmental monitors in remote locations, and it looks like you've done all the hard design work for us already!  Thanks so much for sharing.

Quick question:  how did you end up setting up an "SBD" / Gateway service with Iridium?  Did you use a 9603 module + power circuitry PCB from a reseller, who then provided their own data service to you?

Cheers & thanks so much for your work.

PaulZC, 2017-09-09:
Hi there,
I purchased the 9603 module from AST Systems in the UK and had them set up email forwarding for the SBD messages. They do offer an HTTP service too but I find email better suits my needs. I designed all of the power circuitry etc. myself - you can find full details in the Eagle directory or the pdf files in the repo.
If you want to carry on the conversation, you can contact me here:
https://www.dur.ac.uk/contactperson/?lid=1724
Enjoy!
Paul

PaulZC, 2017-09-16:
Hi,
The Iridium 9603N Beacon repo has just had a major facelift. See https://github.com/PaulZC/Iridium_9603_Beacon/blob/master/LEARN.md for a more detailed description of the beacon - with pictures!
Enjoy!
Paul

dwblair, 2017-09-17:
Paul,

Thanks so much for the revised presentation -- very thoughtful and thorough.  This is really impressive work, and I hope to dig into this week to understand it better.  And -- those light-weight, flexible solar panels are gorgeous :)

Thanks for sharing all of this functionality with the community.  Huge help.

Cheers,
Don

Closed 2017-09-09.

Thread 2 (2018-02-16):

Iridium RX line held high.

keitarusm, 2018-02-16:
Hi, Paul

I've been following your work for a while now and I really want to thank you for your contributions. I've adapted your beacon for use in a sea-ice monitoring buoy. I'm having an issue right now where the RX line of the modem is being held high, the samd21 can't communicate with the modem. For diagnosing this issue I've verified that when the modem is powered down the samd21 can successfully transmit on this line, and similarly if the iridium sleep and 5V are powered on but the modem is not in the socket, then the samd21 can transmit.

I'm certainly not asking you to deep dive on this issue, just wondering if you've seen it before and maybe know the boneheaded mistake I've made. Either way, once I've figured it out I will post the solution here in case it's helpful to anyone else following along with your work.

Again, great stuff. Following your notes on adapting things for this microprocessor has been really instrumental to moving my own work along. My project is also to be released under the same license as yours, just as soon as it actually does something and is useful to the community.

V/r
James Whitlock

PaulZC, 2018-02-16:
Hi James,
I'm very glad you're finding the Beacon design useful.
Can you send me a message via [this link](https://www.dur.ac.uk/contactperson/?lid=1724) so we can take the discussion off-line for now, then - as you suggest - update this issue with the solution.
Best wishes,
Paul

PaulZC, 2018-02-16:
Actually, one thing to check first is:
The TX/RX pins on the 9603N can be confusing... They use old-school DCE notation.
Pin 6 is called "DF_S_TX" but is actually the receive data INPUT. You need to connect this to your Tx pin.
Likewise pin 7 is called "DF_S_RX" but is actually the serial data OUTPUT. You need to connect this to your Rx pin.
If it's not that, then let's continue off-line...

keitarusm, 2018-02-17:
Paul,
This exactly. I should have read the data sheet more carefully. Live and learn. Thank you for the reply.

-James

Closed 2018-02-17.

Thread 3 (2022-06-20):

Is a super capacitor really needed?

saffetblt, 2022-06-20:
Hello Paul,
I like your work, congratulations. I have a question for you. Do you really need a Supercapacitor when using Iridium? I see that 3 serial Energyzer L92 can handle peak currents. Is there something I missed?

Thanks in advance for your answer.

PaulZC, 2022-06-21:
Hello Saffet (@saffetblt ),

The 9603N modem needs 5.0V +/- 10% and draws a peak current of 1.3A when it is transmitting. So long as your power circuit can deliver that then you are good to go.

The super capacitors are useful as they can be charged up slowly from a low current source (such as a solar panel) and then deliver the 1.3A when needed. The charging circuit also "step up" the battery voltage, charging the capacitors to 5.3V. If the batteries get really cold (on a balloon flight) the voltage will fall to about 1.1V per cell. The charging circuit still works, stepping up 3.3V to 5.3V.

On some of my other designs, I used a PP3 (9V) battery and a 5V switching regulator to deliver the current. See:

https://github.com/PaulZC/Iridium_9603N_Mini_Beacon

Good luck with your project!

Best wishes,
Paul

Closed 2022-06-21.

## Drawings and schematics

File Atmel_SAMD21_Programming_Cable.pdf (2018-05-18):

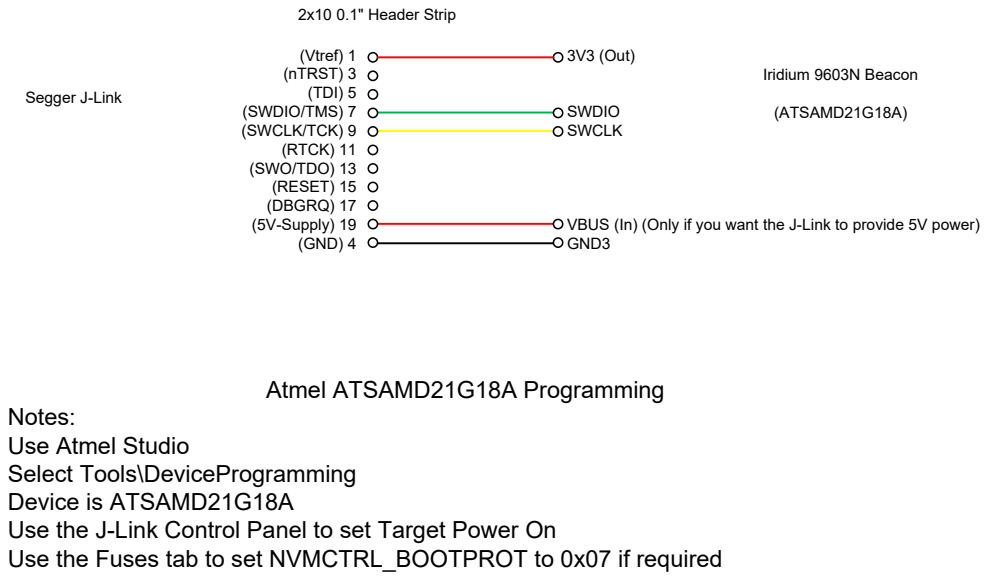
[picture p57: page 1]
Segger J-Link; Atmel ATSAMD21G18A Programming; (Vtref) 1 (nTRST) 3 (TDI) 5 (SWDIO/TMS) 7 (SWCLK/TCK) 9 (RTCK) 11 (SWO/TDO) 13 (RESET) 15 (DBGRQ) 17 (5V-Supply) 19 (GND) 4; Iridium 9603N Beacon; (ATSAMD21G18A); 2x10 0.1" Header Strip; 3V3 (Out); SWDIO SWCLK

VBUS (In) (Only if you want the J-Link to provide 5V power)
GND3

Notes:
Use Atmel Studio
Select Tools\DeviceProgramming
Device is ATSAMD21G18A
Use the J-Link Control Panel to set Target Power On
Use the Fuses tab to set NVMCTRL_BOOTPROT to 0x07 if required

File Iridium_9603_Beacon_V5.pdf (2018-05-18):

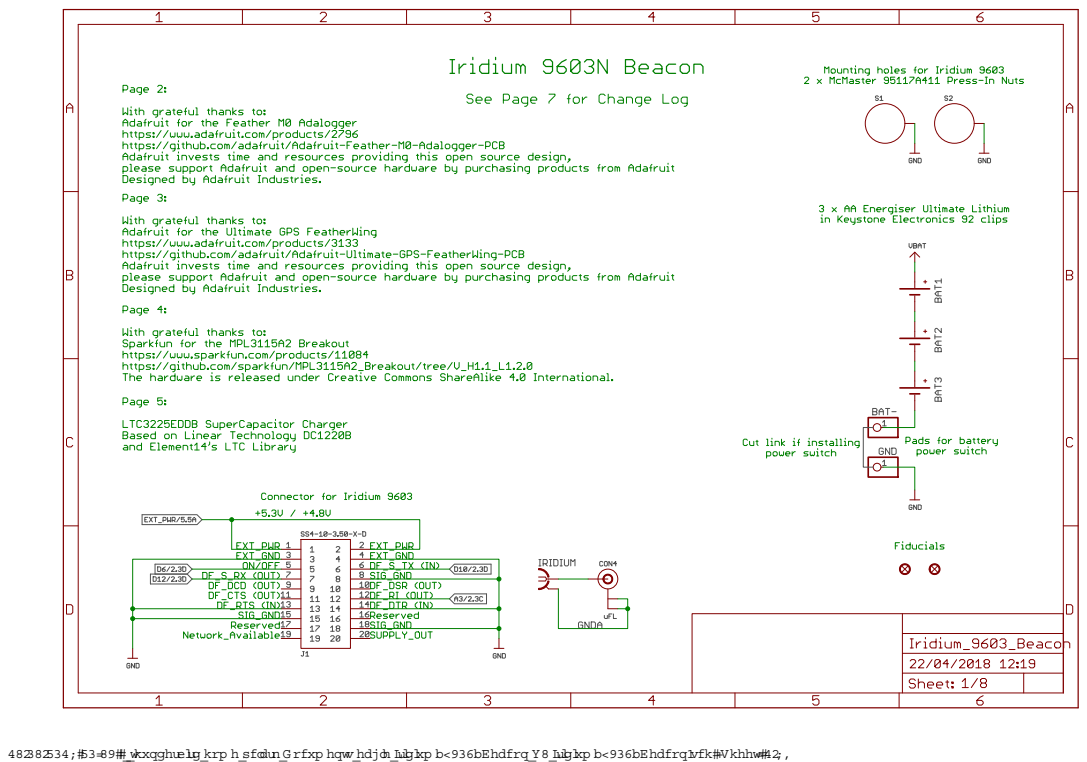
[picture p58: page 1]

thunderbird\hom e\pclark\D ocum ents\eagle\Iridium _9603_Beacon\V5\Iridium _9603_Beacon.sch (Sheet: 1/8)

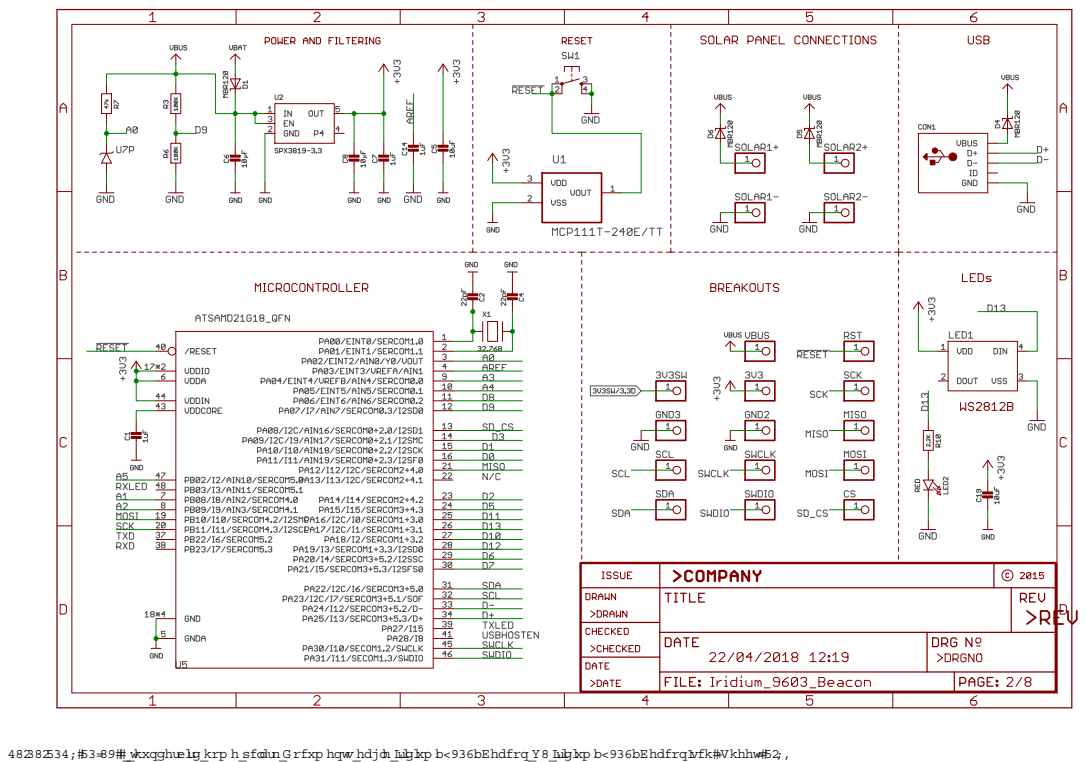
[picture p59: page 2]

thunderbird\hom e\pclark\D ocum ents\eagle\Iridium _9603_Beacon\V5\Iridium _9603_Beacon.sch (Sheet: 2/8)

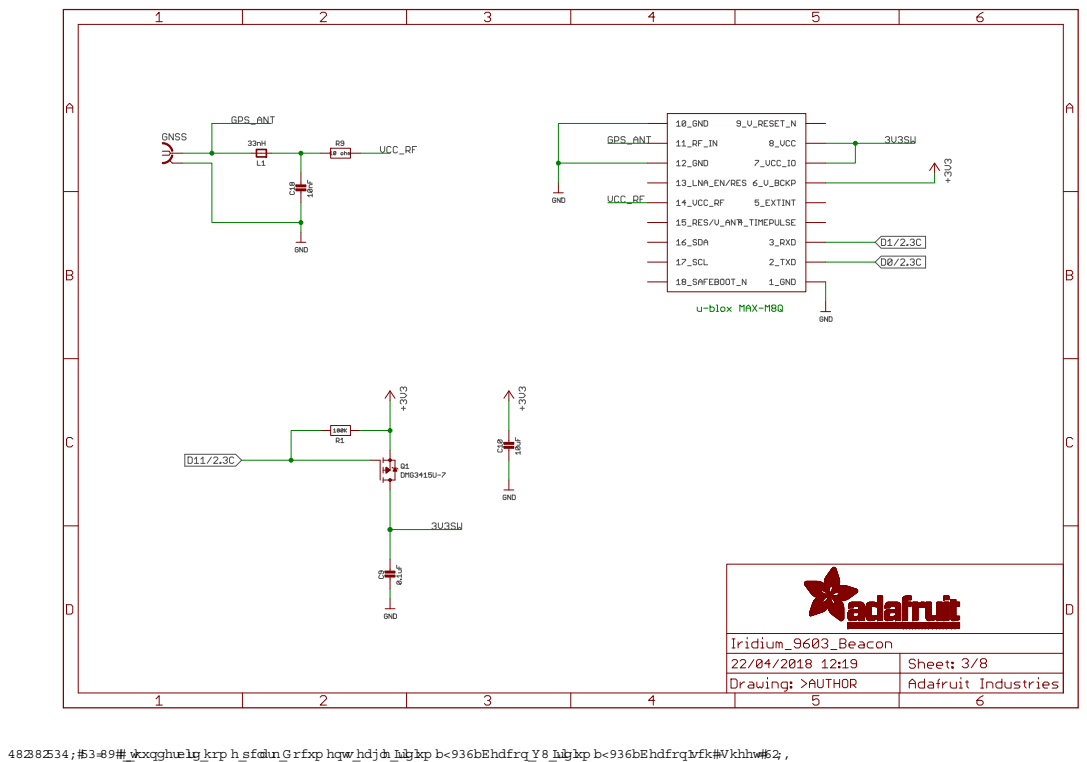
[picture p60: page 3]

thunderbird\hom e\pclark\D ocum ents\eagle\Iridium _9603_Beacon\V5\Iridium _9603_Beacon.sch (Sheet: 3/8)

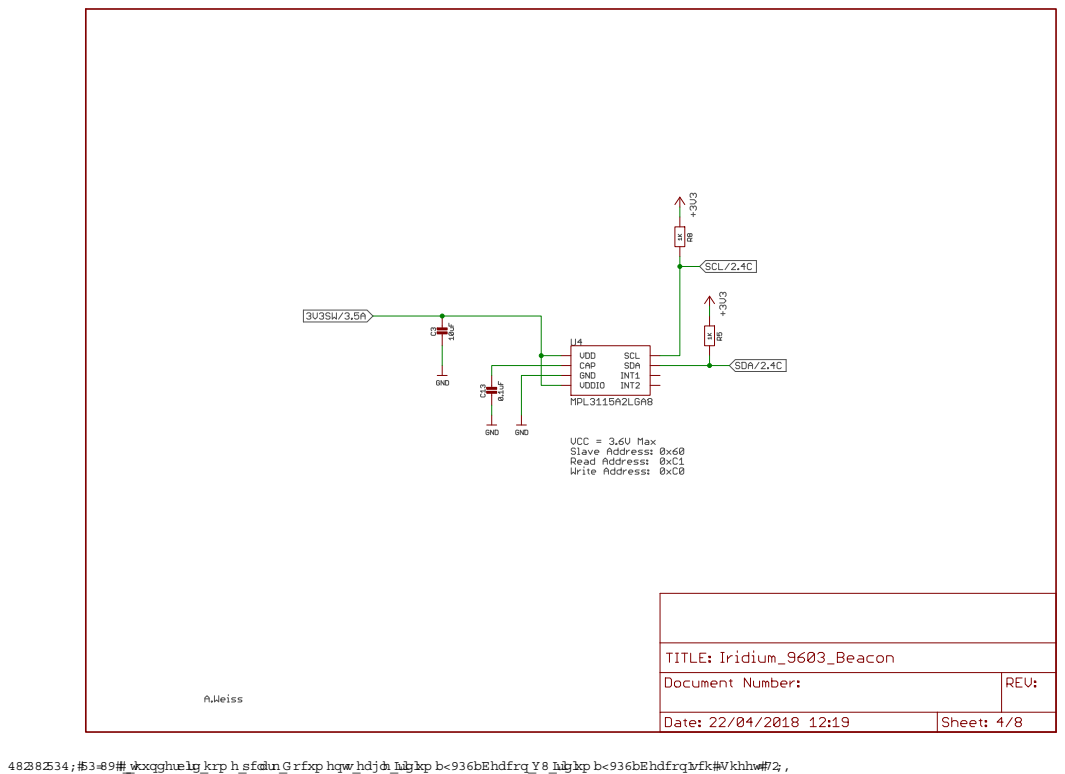
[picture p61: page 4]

thunderbird\hom e\pclark\D ocum ents\eagle\Iridium _9603_Beacon\V5\Iridium _9603_Beacon.sch (Sheet: 4/8)

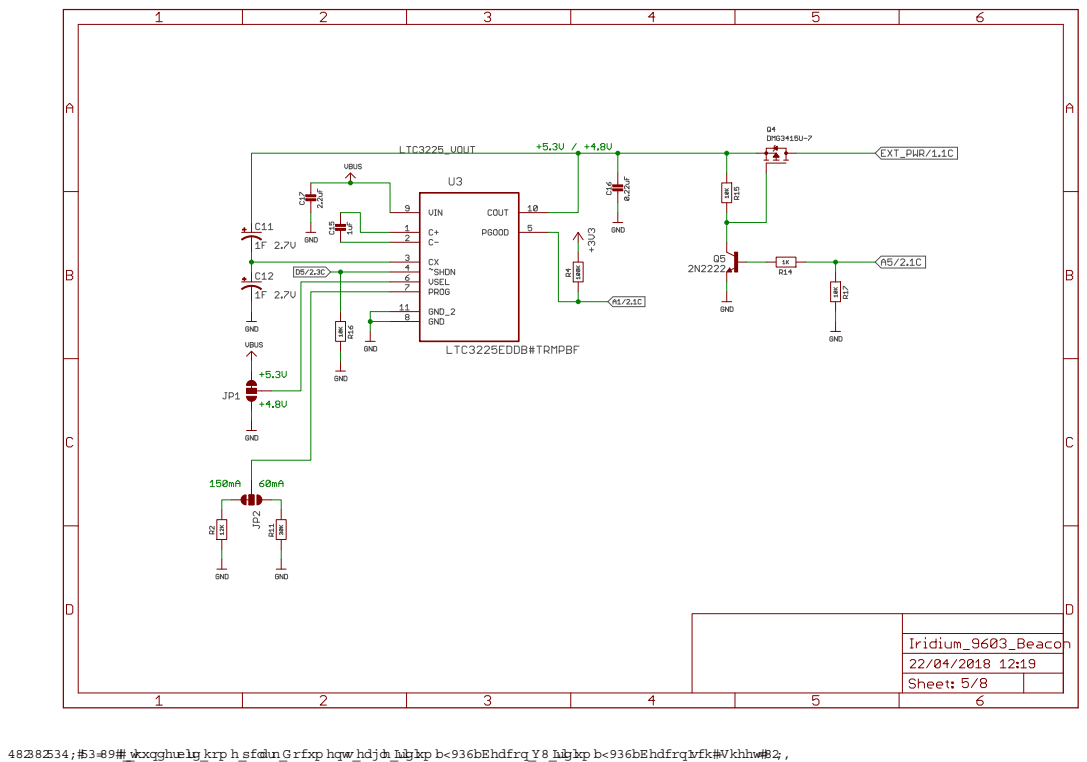
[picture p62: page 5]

thunderbird\hom e\pclark\D ocum ents\eagle\Iridium _9603_Beacon\V5\Iridium _9603_Beacon.sch (Sheet: 5/8)

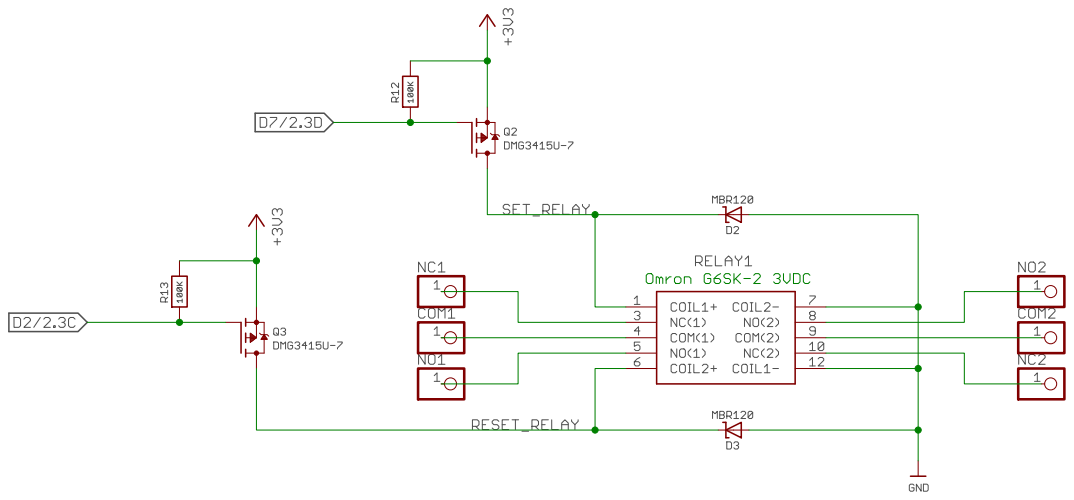
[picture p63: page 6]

thunderbird\hom e\pclark\D ocum ents\eagle\Iridium _9603_Beacon\V5\Iridium _9603_Beacon.sch (Sheet: 6/8)

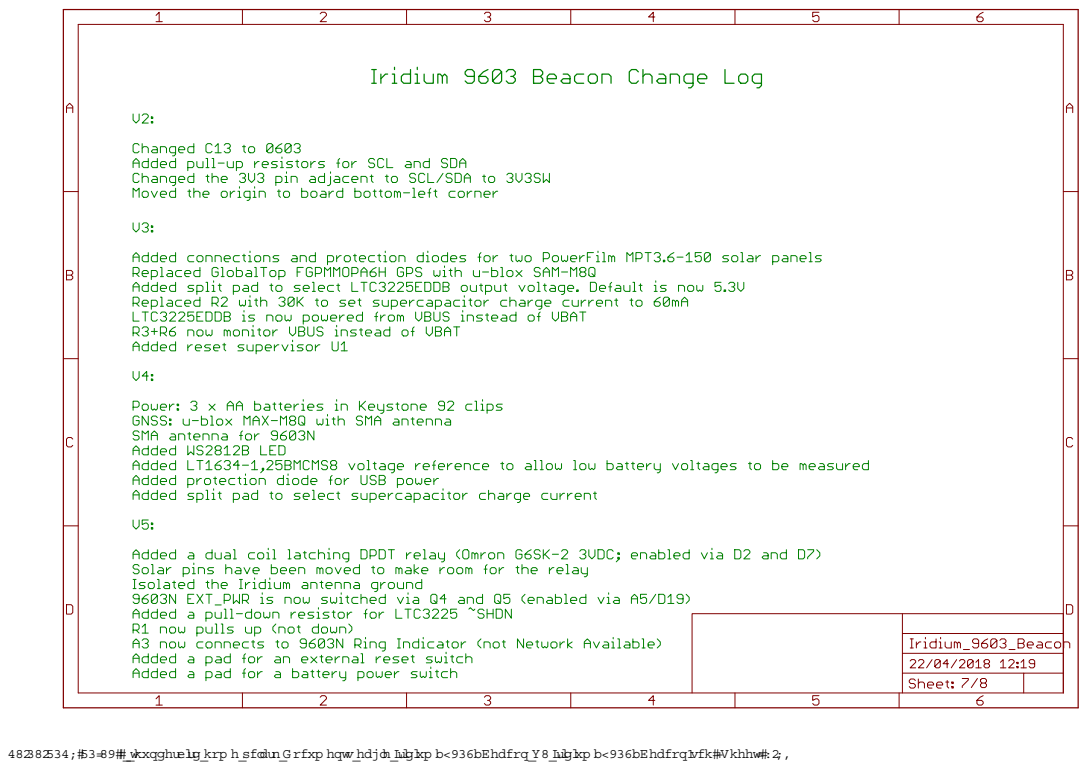
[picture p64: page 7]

thunderbird\hom e\pclark\D ocum ents\eagle\Iridium _9603_Beacon\V5\Iridium _9603_Beacon.sch (Sheet: 7/8)

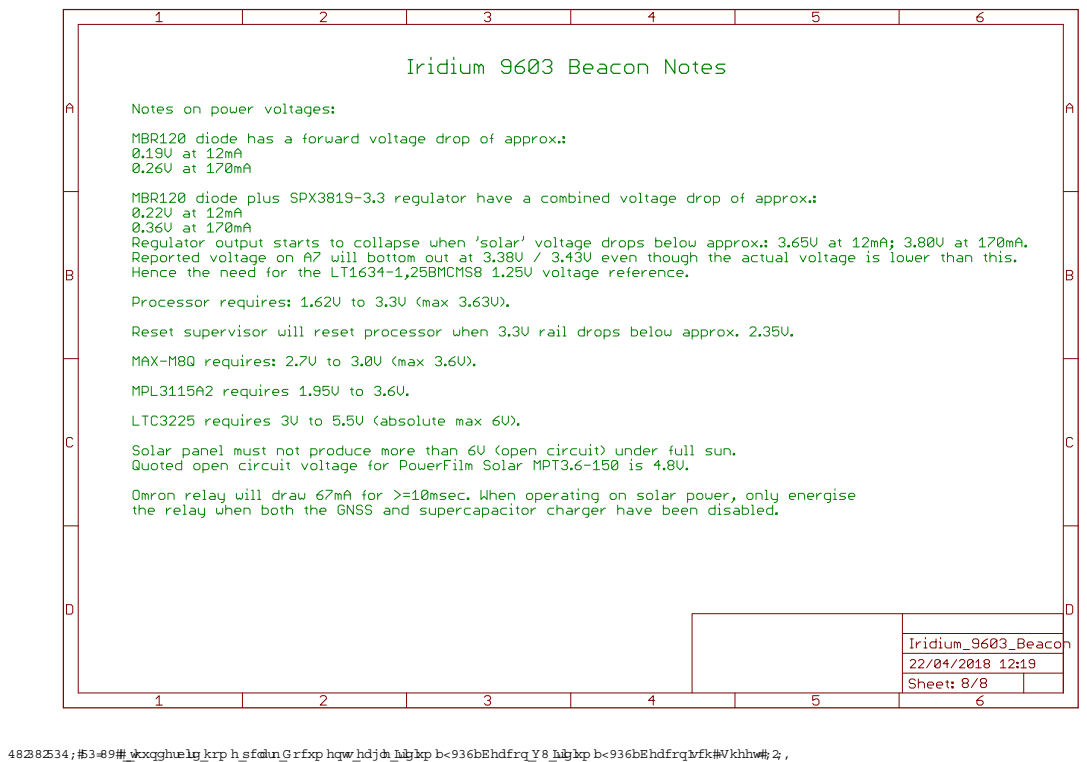
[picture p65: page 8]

thunderbird\hom e\pclark\D ocum ents\eagle\Iridium _9603_Beacon\V5\Iridium _9603_Beacon.sch (Sheet: 8/8)

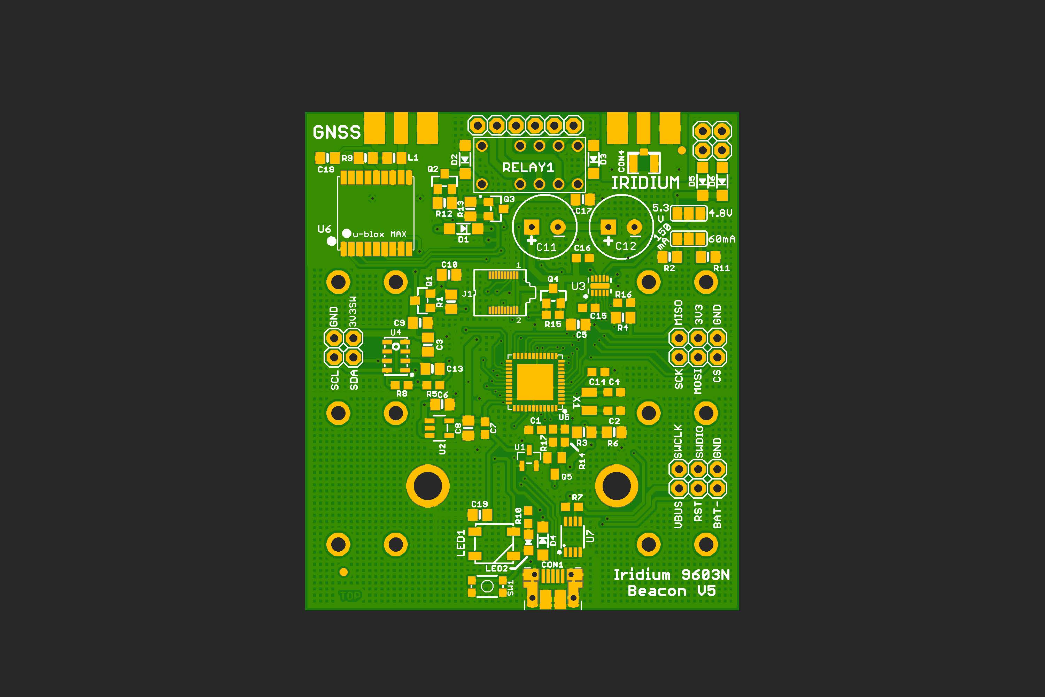
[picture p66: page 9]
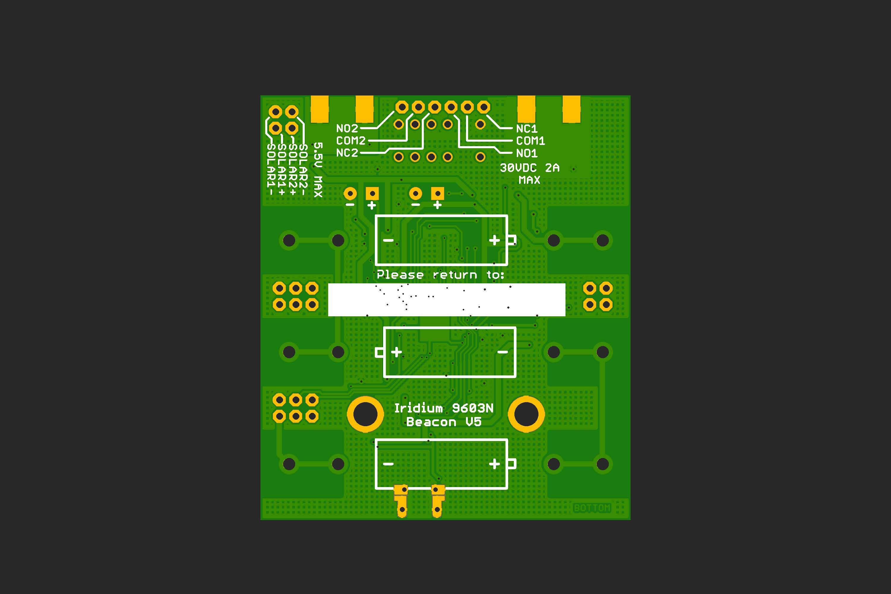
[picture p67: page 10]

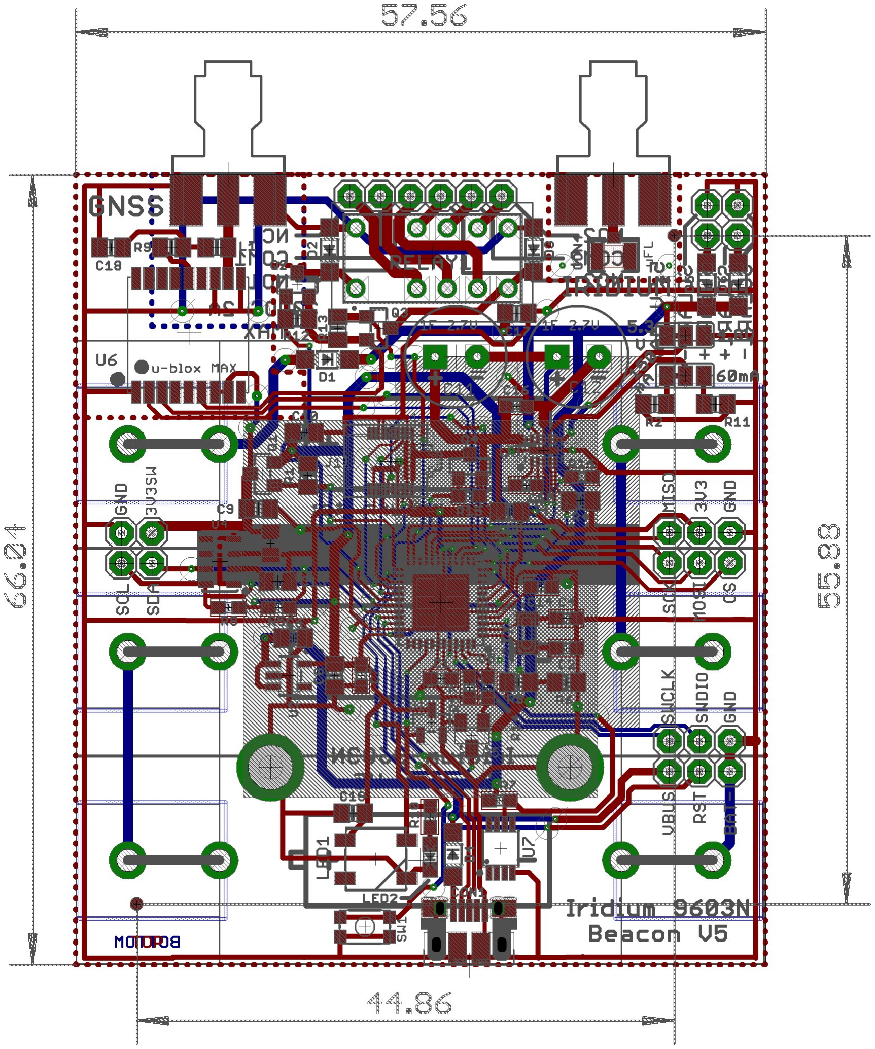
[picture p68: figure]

15/05/2018 20:54 \\thunderbird\home\pclark\Documents\eagle\Iridium_9603_Beacon\V5\Iridium_9603_Beacon.brd

Part | X | Y | Angle Package Value | Manufacturer | Manufacturer Part No

Farnell Part
| | | | | | | No | Mouser Part No

McMaster
Part No | Description | Alternative Part

Dimensions 57.56 66.04

Fiducials - for solder paste mask alignment:

FD1 | 5.08 | 5.08 | 0 | | | | | | Fiducial 1mm
FD2 | 49.94 | 60.96 0 | Fiducial 1mm

Surface Mount Components:

C1 | 30.48 | 23.91 180 | 0603 | 1uF | Walsin | 0603X105K100CT | 2496916 | MultiLayer Ceramic Capacitor; 1uF; 10V; 0603; X5R | 1uF 50V ±10% 0603 Samsung
C7 | 23.81 | 24.16 270 | 0603 | 1uF | Walsin | 0603X105K100CT | 2496916 | MultiLayer Ceramic Capacitor; 1uF; 10V; 0603; X5R | 1uF 50V ±10% 0603 Samsung
C14 | 38.86 | 31.59 0 | 0603 | 1uF | Walsin | 0603X105K100CT | 2496916 | MultiLayer Ceramic Capacitor; 1uF; 10V; 0603; X5R | 1uF 50V ±10% 0603 Samsung
C15 | 37.59 | 40.10 0 | 0603 | 1uF | Walsin | 0603X105K100CT | 2496916 | MultiLayer Ceramic Capacitor; 1uF; 10V; 0603; X5R | 1uF 50V ±10% 0603 Samsung
C2 | 40.96 | 26.45 0 | 0603 | 12pF | Walsin | 0603N120J500CT | 2496884 | MultiLayer Ceramic Capacitor; 12pF; 50V; 0603 | 12pF 50V ±5% 0603 Samsung
C4 | 40.96 | 28.92 0 | 0603 | 12pF | Walsin | 0603N120J500CT | 2496884 | MultiLayer Ceramic Capacitor; 12pF; 50V; 0603 | 12pF 50V ±5% 0603 Samsung
C3 | 16.26 | 35.21 270 | 0805 | 10uF | Walsin | 0805F106Z100CT | 2496998 | MultiLayer Ceramic Capacitor; 10uF; 10V; 0805 | 10uF 16V ±10% 0805 Samsung
C5 | 36.20 | 37.88 180 | 0805 | 10uF | Walsin | 0805F106Z100CT | 2496998 | MultiLayer Ceramic Capacitor; 10uF; 10V; 0805 | 10uF 16V ±10% 0805 Samsung
C6 | 18.16 | 27.30 0 | 0805 | 10uF | Walsin | 0805F106Z100CT | 2496998 | MultiLayer Ceramic Capacitor; 10uF; 10V; 0805 | 10uF 16V ±10% 0805 Samsung
C8 | 21.59 | 24.16 270 | 0805 | 10uF | Walsin | 0805F106Z100CT | 2496998 | MultiLayer Ceramic Capacitor; 10uF; 10V; 0805 | 10uF 16V ±10% 0805 Samsung
C10 | 19.05 | 44.48 0 | 0805 | 10uF | Walsin | 0805F106Z100CT | 2496998 | MultiLayer Ceramic Capacitor; 10uF; 10V; 0805 | 10uF 16V ±10% 0805 Samsung
C19 | 23.15 | 12.67 180 | 0805 | 10uF | Walsin | 0805F106Z100CT | 2496998 | MultiLayer Ceramic Capacitor; 10uF; 10V; 0805 | 10uF 16V ±10% 0805 Samsung
C9 | 15.24 | 38.13 0 | 0805 | 0.1uF | Walsin | 0805B104K500CT | 2496944 | MultiLayer Ceramic Capacitor; 0.1uF; 50V; 0805; X7R | 100nF 50V ±10% 0805 Samsung
C13 | 16.86 | 32.04 0 | 0805 | 0.1uF | Walsin | 0805B104K500CT | 2496944 | MultiLayer Ceramic Capacitor; 0.1uF; 50V; 0805; X7R | 100nF 50V ±10% 0805 Samsung
C16 | 36.77 | 46.70 0 | 0603 | 0.22uF | Multicomp | MC0603F224Z160CT | 1759019 | MultiLayer Ceramic Capacitor; 0.22uF; 16V; 0603 | 220nF 25V ±10% 0603 Samsung
C17 | 36.80 | 54.45 0 | 0805 | 2.2uF | Multicomp | MCTT21X225K100CT | 1759477 | MultiLayer Ceramic Capacitor; 2.2uF; 10V; 0805; X5R | 2.2uF 25V ±10% 0805 Samsung
C18 | 2.95 | 59.94 180 | 0805 | 10nF | Walsin | 0805B103K500CT | 2496939 | MultiLayer Ceramic Capacitor; 10nF; 50V; 0805; X7R | 10nF 50V ±5% 0805 Samsung
CON1 | 32.83 | 2.99 | 0 | Micro_USB | Amphenol_FCI | 10103594 | 2293752 | | Amphenol FCI 10103594 Micro USB Type B | A01SB7X4X1B21-167 Micro USB 5S B
CON4 | 44.89 | 59.98 90 | uFL | uFL | Hirose | U.FL-R-SMT(01) | 3908021 | HIROSE U.FL-R-SMT(01); U.FL Coaxial; Straight Jack; 50 ohm
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

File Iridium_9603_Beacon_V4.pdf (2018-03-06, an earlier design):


thunderbird\hom e\pclark\D ocum ents\eagle\Iridium _9603_Beacon\V4\Iridium _9603_Beacon.sch (Sheet: 1/7)


thunderbird\hom e\pclark\D ocum ents\eagle\Iridium _9603_Beacon\V4\Iridium _9603_Beacon.sch (Sheet: 2/7)


thunderbird\hom e\pclark\D ocum ents\eagle\Iridium _9603_Beacon\V4\Iridium _9603_Beacon.sch (Sheet: 3/7)


thunderbird\hom e\pclark\D ocum ents\eagle\Iridium _9603_Beacon\V4\Iridium _9603_Beacon.sch (Sheet: 4/7)


thunderbird\hom e\pclark\D ocum ents\eagle\Iridium _9603_Beacon\V4\Iridium _9603_Beacon.sch (Sheet: 5/7)


thunderbird\hom e\pclark\D ocum ents\eagle\Iridium _9603_Beacon\V4\Iridium _9603_Beacon.sch (Sheet: 6/7)


thunderbird\hom e\pclark\D ocum ents\eagle\Iridium _9603_Beacon\V4\Iridium _9603_Beacon.sch (Sheet: 7/7)


Part X | Y | Angle Package Value | Manufacturer | Manufacturer Part No

Farnell Part
| | | | | | | No | Mouser Part No | Description
FD1 5.08 | 5.08 | 0 | Fiducial 1mm
FD2 52.48 | 60.96 0 | Fiducial 1mm
C1 | 30.48 | 23.91 180 | 0603 | 1uF | Walsin | 0603X105K100CT | 2496916 | MultiLayer Ceramic Capacitor; 1uF; 10V; 0603; X5R
C2 | 40.96 | 26.45 0 | 0603 | 12pF | Walsin | 0603N120J500CT | 2496884 | MultiLayer Ceramic Capacitor; 12pF; 50V; 0603
C3 | 16.26 | 35.21 270 | 0805 | 10uF | Walsin | 0805F106Z100CT | 2496998 | MultiLayer Ceramic Capacitor; 10uF; 10V; 0805
C4 | 40.96 | 28.92 0 | 0603 | 12pF | Walsin | 0603N120J500CT | 2496884 | MultiLayer Ceramic Capacitor; 12pF; 50V; 0603
C5 | 36.20 | 37.88 180 | 0805 | 10uF | Walsin | 0805F106Z100CT | 2496998 | MultiLayer Ceramic Capacitor; 10uF; 10V; 0805
C6 | 18.16 | 27.30 0 | 0805 | 10uF | Walsin | 0805F106Z100CT | 2496998 | MultiLayer Ceramic Capacitor; 10uF; 10V; 0805
C7 | 23.81 | 24.16 270 | 0603 | 1uF | Walsin | 0603X105K100CT | 2496916 | MultiLayer Ceramic Capacitor; 1uF; 10V; 0603; X5R
C8 | 21.59 | 24.16 270 | 0805 | 10uF | Walsin | 0805F106Z100CT | 2496998 | MultiLayer Ceramic Capacitor; 10uF; 10V; 0805
C9 | 15.24 | 38.13 0 | 0805 | 0.1uF | Walsin | 0805B104K500CT | 2496944 | MultiLayer Ceramic Capacitor; 0.1uF; 50V; 0805; X7R
C10 | 19.05 | 44.48 0 | 0805 | 10uF | Walsin | 0805F106Z100CT | 2496998 | MultiLayer Ceramic Capacitor; 10uF; 10V; 0805
C13 | 16.86 | 32.04 0 | 0805 | 0.1uF | Walsin | 0805B104K500CT | 2496944 | MultiLayer Ceramic Capacitor; 0.1uF; 50V; 0805; X7R
C14 | 38.86 | 31.59 0 | 0603 | 1uF | Walsin | 0603X105K100CT | 2496916 | MultiLayer Ceramic Capacitor; 1uF; 10V; 0603; X5R
C15 | 37.59 | 40.10 0 | 0603 | 1uF | Walsin | 0603X105K100CT | 2496916 | MultiLayer Ceramic Capacitor; 1uF; 10V; 0603; X5R
C16 | 36.77 | 46.70 0 | 0603 | 0.22uF | Multicomp | MC0603F224Z160CT | 1759019 | MultiLayer Ceramic Capacitor; 0.22uF; 16V; 0603
C17 | 36.86 | 55.05 0 | 0805 | 2.2uF | Multicomp | MCTT21X225K100CT | 1759477 | MultiLayer Ceramic Capacitor; 2.2uF; 10V; 0805; X5R
C18 | 2.95 | 59.94 180 | 0805 | 10nF | Walsin | 0805B103K500CT | 2496939 | MultiLayer Ceramic Capacitor; 10nF; 50V; 0805; X7R
C19 | 23.15 | 12.67 180 | 0805 | 10uF | Walsin | 0805F106Z100CT | 2496998 | MultiLayer Ceramic Capacitor; 10uF; 10V; 0805
CON1 32.83 | 2.99 | 0 | Micro_USB | Amphenol_FCI | 10103594 | 2293752 | Amphenol FCI 10103594 Micro USB Type B
CON4 44.89 | 59.98 90 | uFL | uFL | Hirose | U.FL-R-SMT(01) | 3908021 | HIROSE U.FL-R-SMT(01); U.FL Coaxial; Straight Jack; 50 ohm
D1 | 20.99 | 53.12 180 | SOD-123 MBR120 | ON SEMICONDUCTOR MBR120VLSFT1G | 1431044 | Schottky Rectifier; 20V; 1A; SOD-123
D2 | 21.56 | 57.15 90 | SOD-123 MBR120 | ON SEMICONDUCTOR MBR120VLSFT1G | 1431044 | Schottky Rectifier; 20V; 1A; SOD-123
D3 | 25.43 | 57.18 90 | SOD-123 MBR120 | ON SEMICONDUCTOR MBR120VLSFT1G | 1431044 | Schottky Rectifier; 20V; 1A; SOD-123
D4 | 31.50 | 9.21 | 270 | SOD-123 MBR120 | ON SEMICONDUCTOR MBR120VLSFT1G | 1431044 | Schottky Rectifier; 20V; 1A; SOD-123
J1 | 26.27 | 42.10 0 | SS4-10-3.50 | Samtec | SS4-10-3.50-L-D-K-TR | 2085336 | Samtec SS4-10-3.50-L-D-K-TR
L1 | 11.78 | 59.98 0 | 0805 | 33nH | Coilcraft | 0805HT-33NTGLB | 2286465 | Surface Mount High Frequency Inductor; 0805; 33 nH; 600 mA
LED1 25.05 | 8.83 | 0 | WS2812B | Sparkfun / Worldsemi WS2812B | 474-COM-13667 | RGB LED with Driver
LED2 29.59 | 9.02 | 180 | 2.0x1.25 RED | Multicomp | 703-0107 | 2112119 | LED; Red; 20mA; 2.2V; 2.0x1.25mm
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

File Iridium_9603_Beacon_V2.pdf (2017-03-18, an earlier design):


18/03/2017 13:39 \\thunderbird\home\pclark\Documents\eagle\Iridium_9603_Beacon\V2\Iridium_9603_Beacon.sch (Sheet: 1/6)

OUT 5; GND 2; GND 18*4; VDDA 6; PA16/I2C/I0/SERCOM1+3.0; PA17/I2C/I1/SERCOM1+3.1; PA18/I2/SERCOM1+3.2; PA19/I3/SERCOM1+3.3/I2SD0; PA22/I2C/I6/SERCOM3+5.0; PA23/I2C/I7/SERCOM3+5.1/SOF; PA24/I12/SERCOM3+5.2/D-; PA25/I13/SERCOM3+5.3/D+; PA30/I10/SECOM1.2/SWCLK; PA31/I11/SECOM1.3/SWDIO; PA09/I2C/I9/AIN17/SERCOM0+2.1/I2SMC; 14 PA08/I2C/AIN16/SERCOM0+2.0/I2SD1; PA15/I15/SERCOM3+4.3; PA11/I11/AIN19/SERCOM0+2.3/I2SF0; PA14/I14/SERCOM2+4.2; PA10/I10/AIN18/SERCOM0+2.2/I2SCK; /RESET 40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

18/03/2017 13:39 \\thunderbird\home\pclark\Documents\eagle\Iridium_9603_Beacon\V2\Iridium_9603_Beacon.sch (Sheet: 2/6)

1PPS P$13; 3D-FIX P$5; EX_ANT P$11; GND P$3; GND P$8; GND P$12; GND P$19; NRESET P$2; RTCM P$14; VBACKUP P$4; VCC P$1

18/03/2017 13:39 \\thunderbird\home\pclark\Documents\eagle\Iridium_9603_Beacon\V2\Iridium_9603_Beacon.sch (Sheet: 3/6)

VDD 1 CAP 2 GND 3 VDDIO 4; SCL; SDA; INT1; INT2

18/03/2017 13:39 \\thunderbird\home\pclark\Documents\eagle\Iridium_9603_Beacon\V2\Iridium_9603_Beacon.sch (Sheet: 4/6)

VIN 9; CX 3 ~SHDN 4 VSEL 6 PROG 7; GND_2 11 GND 8; COUT; PGOOD

18/03/2017 13:39 \\thunderbird\home\pclark\Documents\eagle\Iridium_9603_Beacon\V2\Iridium_9603_Beacon.sch (Sheet: 5/6)


18/03/2017 13:39 \\thunderbird\home\pclark\Documents\eagle\Iridium_9603_Beacon\V2\Iridium_9603_Beacon.sch (Sheet: 6/6)

Part X Y

Angle
(wrt
Eagle
Lib!) | Package Value | Manufacturer | Manufacturer Part No

Farnell Part
No | Mouser Part No

McMaster Part
No | Adafruit / ProtoPic Description
FD1 | 7.62 | 7.62 | 0 | | | | | | Fiducial
FD2 | 43.18 | 53.34 0 | Fiducial
C1 | 26.99 | 19.43 180 | 0603 | 1uF | Walsin | 0603X105K100CT | 2496916 | MultiLayer Ceramic Capacitor; 1uF; 10V; 0603; X5R
C2 | 37.47 | 21.97 0 | 0603 | 12pF | Walsin | 0603N120J500CT | 2496884 | MultiLayer Ceramic Capacitor; 12pF; 50V; 0603
C3 | 12.76 | 30.73 270 | 0805 | 10uF | Walsin | 0805F106Z100CT | 2496998 | MultiLayer Ceramic Capacitor; 10uF; 10V; 0805
C4 | 37.47 | 24.45 0 | 0603 | 12pF | Walsin | 0603N120J500CT | 2496884 | MultiLayer Ceramic Capacitor; 12pF; 50V; 0603
C5 | 32.7 | 33.4 | 180 | 0805 | 10uF | Walsin | 0805F106Z100CT | 2496998 | MultiLayer Ceramic Capacitor; 10uF; 10V; 0805
C6 | 7.94 | 19.69 270 | 0805 | 10uF | Walsin | 0805F106Z100CT | 2496998 | MultiLayer Ceramic Capacitor; 10uF; 10V; 0805
C7 | 20.32 | 19.69 270 | 0603 | 1uF | Walsin | 0603X105K100CT | 2496916 | MultiLayer Ceramic Capacitor; 1uF; 10V; 0603; X5R
C8 | 18.1 | 19.69 270 | 0805 | 10uF | Walsin | 0805F106Z100CT | 2496998 | MultiLayer Ceramic Capacitor; 10uF; 10V; 0805
C9 | 11.75 | 33.66 0 | 0805 | 0.1uF | Walsin | 0805B104K500CT | 2496944 | MultiLayer Ceramic Capacitor; 0.1uF; 50V; 0805; X7R
C10 | 15.56 | 40.01 0 | 0805 | 10uF | Walsin | 0805F106Z100CT | 2496998 | MultiLayer Ceramic Capacitor; 10uF; 10V; 0805
C13 | 13.46 | 27.56 0 | 0603 | 0.1uF | Walsin | 0603B104K500CT | 2496834 | MultiLayer Ceramic Capacitor; 0.1uF; 50V; 0603; X7R
C14 | 35.37 | 27.11 0 | 0603 | 1uF | Walsin | 0603X105K100CT | 2496916 | MultiLayer Ceramic Capacitor; 1uF; 10V; 0603; X5R
C15 | 34.1 | 35.62 0 | 0603 | 1uF | Walsin | 0603X105K100CT | 2496916 | MultiLayer Ceramic Capacitor; 1uF; 10V; 0603; X5R
C16 | 33.27 | 42.23 0 | 0603 | 0.22uF | Multicomp | MC0603F224Z160CT | 1759019 | MultiLayer Ceramic Capacitor; 0.22uF; 16V; 0603
C17 | 33.21 | 50.55 0 | 0805 | 2.2uF | Multicomp | MCTT21X225K100CT | 1759477 | MultiLayer Ceramic Capacitor; 2.2uF; 10V; 0805; X5R
CON1 29.34 | 2.99 | 0 | Micro_USB | Amphenol_FCI | 10103594 | 2293752 | Amphenol FCI 10103594 Micro USB Type B
D1 | 9.46 | 23.11 180 | SOD-123 MBR120 | ON SEMICONDUCTOR MBR120VLSFT1G | 1431044 | Schottky Rectifier; 20V; 1A; SOD-123
J1 | 22.78 | 37.63 0 | SS4-10-3.50 | Samtec | SS4-10-3.50-L-D-K-TR | 2085336 | Samtec SS4-10-3.50-L-D-K-TR
LED1 32.64 | 52.96 270 | 2.0x1.25 RED | Multicomp | 703-0107 | 2112119 | LED; Red; 20mA; 2.2V; 2.0x1.25mm
LED2 19.05 | 3.49 | 180 | 2.0x1.25 RED | Multicomp | 703-0107 | 2112119 | LED; Red; 20mA; 2.2V; 2.0x1.25mm
Q1 | 11.75 | 37.47 90 | SOT23 | DMG3415U-7 | Diodes Inc. | DMG3415U-7 | 1843688 | MOSFET; P Channel; SOT23-WIDE
R1 | 10.48 | 19.69 270 | 0603 | 100k | Yageo | RC0603FR-13100KL | 2309107 | Chip Resistor; Thick Film; 100k; 50V; 0603; 100mW
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

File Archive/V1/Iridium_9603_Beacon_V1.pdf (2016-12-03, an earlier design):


20/09/2016 21:12 C:\Users\pclark\Documents\eagle\Iridium_9603_Beacon\Iridium_9603_Beacon.sch (Sheet: 1/5)

OUT 5; GND 2; GND 18*4; VDDA 6; PA16/I2C/I0/SERCOM1+3.0; PA17/I2C/I1/SERCOM1+3.1; PA18/I2/SERCOM1+3.2; PA19/I3/SERCOM1+3.3/I2SD0; PA22/I2C/I6/SERCOM3+5.0; PA23/I2C/I7/SERCOM3+5.1/SOF; PA24/I12/SERCOM3+5.2/D-; PA25/I13/SERCOM3+5.3/D+; PA30/I10/SECOM1.2/SWCLK; PA31/I11/SECOM1.3/SWDIO; PA09/I2C/I9/AIN17/SERCOM0+2.1/I2SMC; 14 PA08/I2C/AIN16/SERCOM0+2.0/I2SD1; PA15/I15/SERCOM3+4.3; PA11/I11/AIN19/SERCOM0+2.3/I2SF0; PA14/I14/SERCOM2+4.2; PA10/I10/AIN18/SERCOM0+2.2/I2SCK; /RESET 40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

20/09/2016 21:12 C:\Users\pclark\Documents\eagle\Iridium_9603_Beacon\Iridium_9603_Beacon.sch (Sheet: 2/5)

1PPS P$13; 3D-FIX P$5; EX_ANT P$11; GND P$3; GND P$8; GND P$12; GND P$19; NRESET P$2; RTCM P$14; VBACKUP P$4; VCC P$1

20/09/2016 21:12 C:\Users\pclark\Documents\eagle\Iridium_9603_Beacon\Iridium_9603_Beacon.sch (Sheet: 3/5)

VDD 1 CAP 2 GND 3 VDDIO 4; SCL; SDA; INT1; INT2

20/09/2016 21:12 C:\Users\pclark\Documents\eagle\Iridium_9603_Beacon\Iridium_9603_Beacon.sch (Sheet: 4/5)

VIN 9; CX 3 ~SHDN 4 VSEL 6 PROG 7; GND_2 11 GND 8; COUT; PGOOD

20/09/2016 21:12 C:\Users\pclark\Documents\eagle\Iridium_9603_Beacon\Iridium_9603_Beacon.sch (Sheet: 5/5)

Part | X | Y

Angle (wrt
Eagle Lib!) Package | Value | Manufacturer | Manufacturer Part No | Farnell Part No | Mouser Part No | McMaster Part No Adafruit / ProtoPic Description
FD1 | 8.89 | 9.72 | 0 | Fiducial
FD2 | 44.45 | 55.44 | 0 | Fiducial
C1 | 28.26 | 21.53 | 180 | 0603 | 1uF | Walsin | 0603X105K100CT | 2496916 | MultiLayer Ceramic Capacitor; 1uF; 10V; 0603; X5R
C2 | 38.73 | 24.07 | 0 | 0603 | 12pF | Walsin | 0603N120J500CT | 2496884 | MultiLayer Ceramic Capacitor; 12pF; 50V; 0603
C3 | 15.56 | 32.26 | 270 | 0805 | 10uF | Walsin | 0805F106Z100CT | 2496998 | MultiLayer Ceramic Capacitor; 10uF; 10V; 0805
C4 | 38.73 | 26.54 | 0 | 0603 | 12pF | Walsin | 0603N120J500CT | 2496884 | MultiLayer Ceramic Capacitor; 12pF; 50V; 0603
C5 | 33.97 | 35.5 | 180 | 0805 | 10uF | Walsin | 0805F106Z100CT | 2496998 | MultiLayer Ceramic Capacitor; 10uF; 10V; 0805
C6 | 9.21 | 21.78 | 270 | 0805 | 10uF | Walsin | 0805F106Z100CT | 2496998 | MultiLayer Ceramic Capacitor; 10uF; 10V; 0805
C7 | 21.59 | 21.78 | 270 | 0603 | 1uF | Walsin | 0603X105K100CT | 2496916 | MultiLayer Ceramic Capacitor; 1uF; 10V; 0603; X5R
C8 | 19.37 | 21.78 | 270 | 0805 | 10uF | Walsin | 0805F106Z100CT | 2496998 | MultiLayer Ceramic Capacitor; 10uF; 10V; 0805
C9 | 13.02 | 35.75 | 0 | 0805 | 0.1uF | Walsin | 0805B104K500CT | 2496944 | MultiLayer Ceramic Capacitor; 0.1uF; 50V; 0805; X7R
C10 | 16.83 | 42.1 | 0 | 0805 | 10uF | Walsin | 0805F106Z100CT | 2496998 | MultiLayer Ceramic Capacitor; 10uF; 10V; 0805
C13 | 15.56 | 29.4 | 0 | 0402 | 0.1uF | TDK | CGA2B3X7R1H104K050BB 2210822 | MultiLayer Ceramic Capacitor; 0.1uF; 50V; 0402
C14 | 36.64 | 29.21 | 0 | 0603 | 1uF | Walsin | 0603X105K100CT | 2496916 | MultiLayer Ceramic Capacitor; 1uF; 10V; 0603; X5R
C15 | 35.37 | 37.72 | 0 | 0603 | 1uF | Walsin | 0603X105K100CT | 2496916 | MultiLayer Ceramic Capacitor; 1uF; 10V; 0603; X5R
C16 | 34.54 | 44.32 | 0 | 0603 | 0.22uF | Multicomp | MC0603F224Z160CT | 1759019 | MultiLayer Ceramic Capacitor; 0.22uF; 16V; 0603
C17 | 34.48 | 52.64 | 0 | 0805 | 2.2uF | Multicomp | MCTT21X225K100CT | 1759477 | MultiLayer Ceramic Capacitor; 2.2uF; 10V; 0805; X5R
CON1 | 30.61 | 5.08 | 0 | Micro_USB | Amphenol_FCI | 10103594 | 2293752 | Amphenol FCI 10103594 Micro USB Type B
D1 | 10.48 | 26.86 | 180 | SOD-123 MBR120 | ON SEMICONDUCTOR | MBR120VLSFT1G | 1431044 | Schottky Rectifier; 20V; 1A; SOD-123
J1 | 24.05 | 39.72 | 0 | SS4-10-3.50 | Samtec | SS4-10-3.50-L-D-K-TR | 2085336 | Samtec SS4-10-3.50-L-D-K-TR
LED1 | 33.91 | 55.05 | 270 | 2.0x1.25 | RED | Multicomp | 703-0107 | 2112119 | LED; Red; 20mA; 2.2V; 2.0x1.25mm
LED2 | 20.32 | 5.59 | 180 | 2.0x1.25 | RED | Multicomp | 703-0107 | 2112119 | LED; Red; 20mA; 2.2V; 2.0x1.25mm
Q1 | 13.02 | 39.56 | 90 | SOT23 | DMG3415U-7 | Diodes Inc. | DMG3415U-7 | 1843688 | MOSFET; P Channel; SOT23-WIDE
R1 | 11.75 | 21.78 | 270 | 0603 | 100k | Yageo | RC0603FR-13100KL | 2309107 | Chip Resistor; Thick Film; 100k; 50V; 0603; 100mW
R2 | 40.7 | 42.04 | 90 | 0805 | 12K | Panasonic | ERJ6ENF1202V | 2303661 | Chip Resistor; Thick Film; 12k; 150V; 0805; 125mW
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

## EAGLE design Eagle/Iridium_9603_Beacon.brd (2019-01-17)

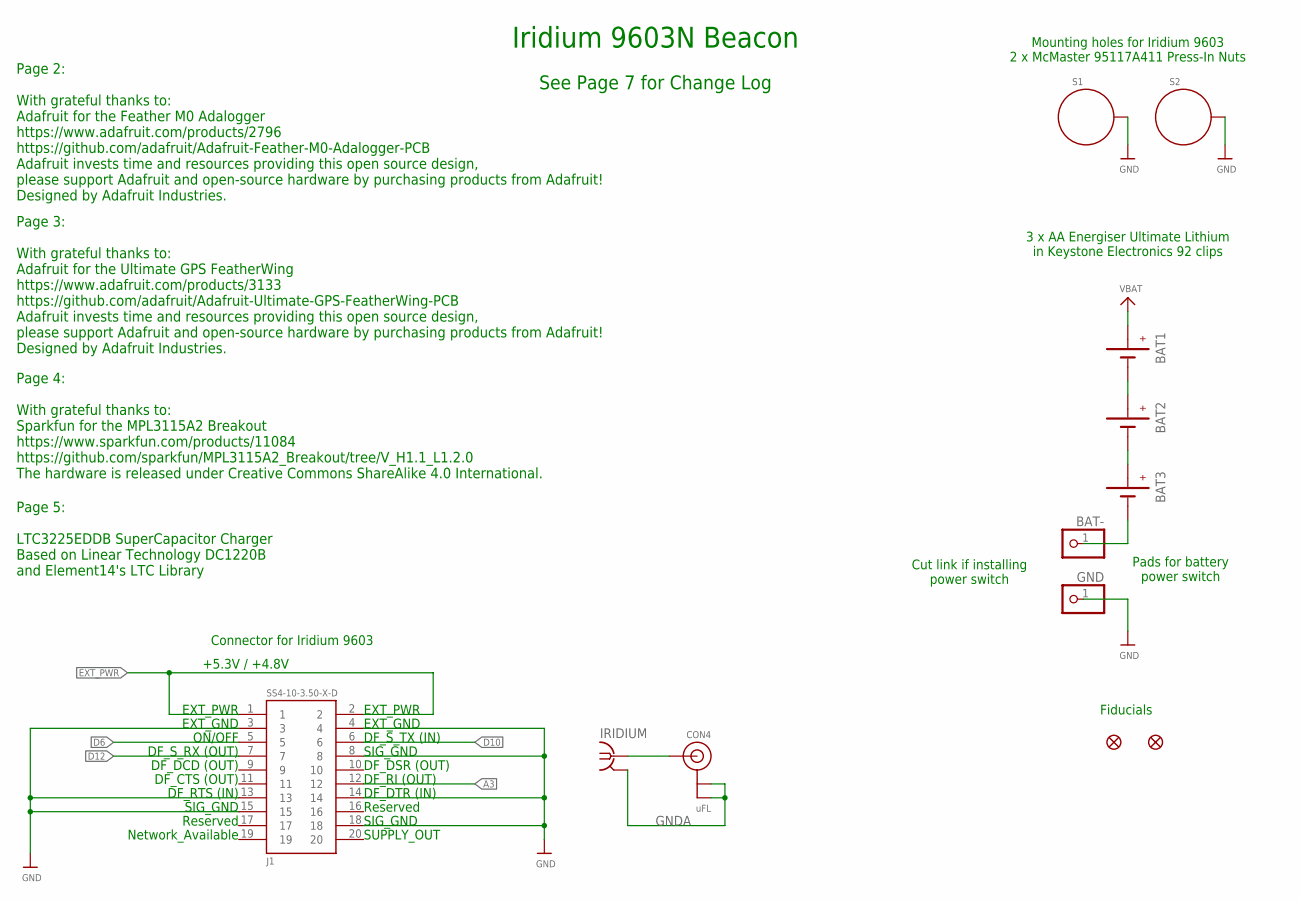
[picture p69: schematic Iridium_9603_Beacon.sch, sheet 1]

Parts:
BAT1, BAT2, BAT3: BATTERYKEYSTONE92; BATTERY-AAA-KEYSTONE92
BAT-: PINHD-1X1; 1X01
CON4: uFL; U.FL
FD1, FD2: FIDUCIAL1X2; FIDUCIAL-1X2
GND: PINHD-1X1; 1X01
IRIDIUM: SMA-142-0711-821/826; J502-ND-142-0711-821/826
J1: SS4-10-3.50-X-D
S1, S2: STANDOFF_ELECTRICALMCMASTER-95117A411; STANDOFF-ELECTRICAL-MCMASTER-95117A411

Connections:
A3: J1.12; also elsewhere on the board
D6: J1.5; also elsewhere on the board
D10: J1.6; also elsewhere on the board
D12: J1.7; also elsewhere on the board
EXT_PWR: J1.1, J1.2; also elsewhere on the board
GND: GND.1, J1.3, J1.4, J1.8, J1.13, J1.14, J1.15, J1.18, S1.P1, S2.P1; also elsewhere on the board
GNDA: CON4.1 (GND), CON4.2 (GND), IRIDIUM.G@1 (2), IRIDIUM.G@2 (2), IRIDIUM.G@3 (2), IRIDIUM.G@4 (2)
unnamed: CON4.3 (SIGNAL), IRIDIUM.1
unnamed: BAT1.GND@1 (-), BAT1.GND@2 (-), BAT2.PWR@1 (+), BAT2.PWR@2 (+)
unnamed: BAT3.GND@1 (-), BAT3.GND@2 (-), BAT-.1
unnamed: BAT2.GND@1 (-), BAT2.GND@2 (-), BAT3.PWR@1 (+), BAT3.PWR@2 (+)
VBAT: BAT1.PWR@1 (+), BAT1.PWR@2 (+); also elsewhere on the board

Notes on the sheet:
3 x AA Energiser Ultimate Lithium in Keystone Electronics 92 clips
Connector for Iridium 9603
Mounting holes for Iridium 9603 2 x McMaster 95117A411 Press-In Nuts
Iridium 9603N Beacon
Page 2: With grateful thanks to: Adafruit for the Feather M0 Adalogger https://www.adafruit.com/products/2796 https://github.com/adafruit/Adafruit-Feather-M0-Adalogger-PCB Adafruit invests time and resources providing this open source design, please support Adafruit and open-source hardware by purc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
Page 3: With grateful thanks to: Adafruit for the Ultimate GPS FeatherWing https://www.adafruit.com/products/3133 https://github.com/adafruit/Adafruit-Ultimate-GPS-FeatherWing-PCB Adafruit invests time and resources providing this open source design, please support Adafruit and open-source hardware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
Page 4: With grateful thanks to: Sparkfun for the MPL3115A2 Breakout https://www.sparkfun.com/products/11084 https://github.com/sparkfun/MPL3115A2_Breakout/tree/V_H1.1_L1.2.0 The hardware is released under Creative Commons ShareAlike 4.0 International.
EXT_PWR
EXT_GND
ON/OFF
DF_S_RX (OUT)
DF_DCD (OUT)
DF_CTS (OUT)
DF_RTS (IN)
SIG_GND
Reserved
Network_Available
DF_S_TX (IN)
DF_DSR (OUT)
DF_RI (OUT)
DF_DTR (IN)
SUPPLY_OUT
Page 5: LTC3225EDDB SuperCapacitor Charger Based on Linear Technology DC1220B and Element14's LTC Library
+5.3V / +4.8V
Fiducials
See Page 7 for Change Log
Pads for battery power switch
Cut link if installing power switch

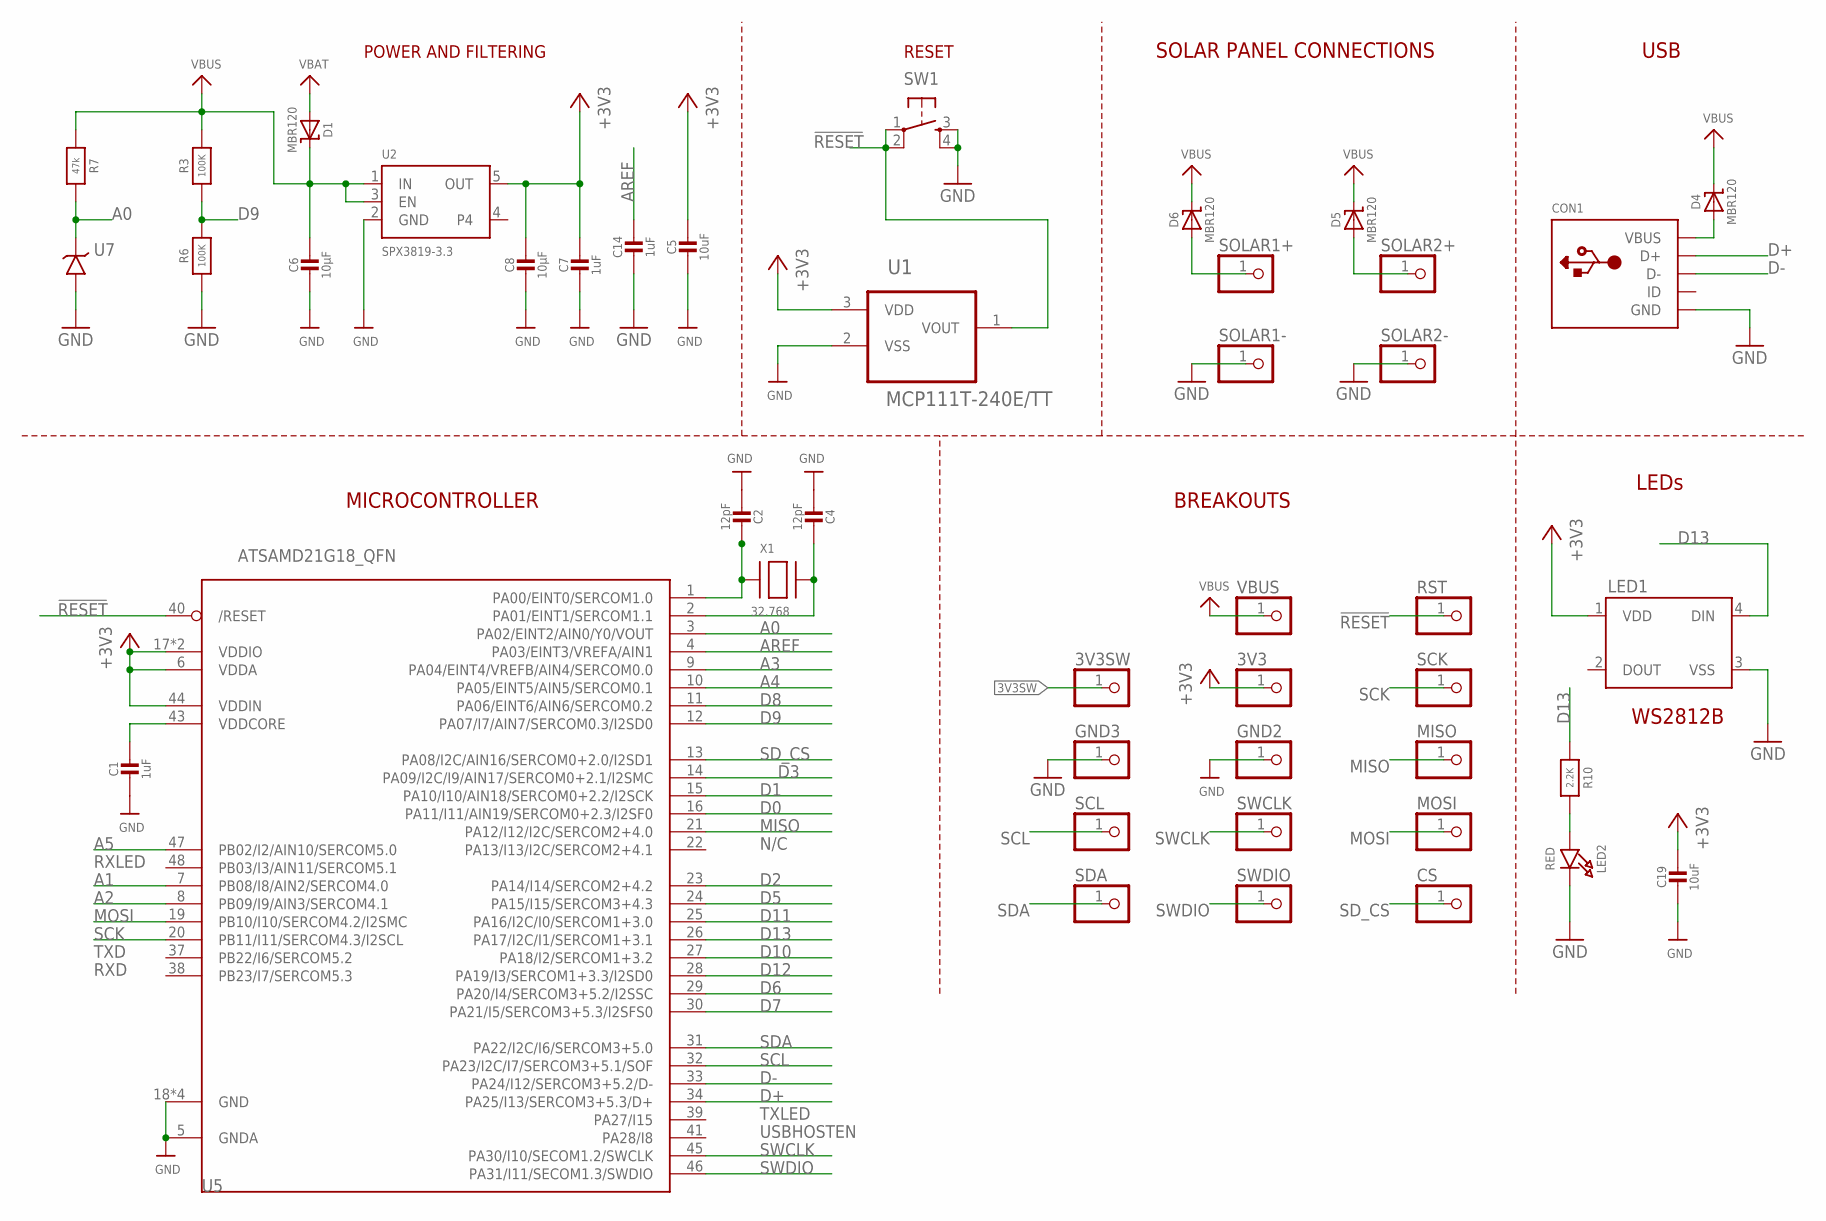
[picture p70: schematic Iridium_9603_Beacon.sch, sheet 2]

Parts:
3V3, 3V3SW: PINHD-1X1; 1X01
C1, C7, C14: 1uF; 0603-NO
C2, C4: 12pF; 0603-NO
C5, C19: 10uF; 0805-NO
C6, C8: 10µF; 0805-NO
CON1: MICROBUILDER_USBFCI_10103594_CORRECTED; MICROBUILDER_FCI_10103594_CORRECTED
CS: PINHD-1X1; 1X01
D1, D4, D5, D6: MBR120; SOD-123
GND2, GND3: PINHD-1X1; 1X01
LED1: WS2812B
LED2: RED; CHIPLED_0805_NOOUTLINE
MISO: PINHD-1X1; 1X01
MOSI: PINHD-1X1; 1X01
R3, R6: 100K; 0805-NO
R7: 47k; 0603-NO
R10: 2.2K; 0603-NO
RST: PINHD-1X1; 1X01
SCK: PINHD-1X1; 1X01
SCL: PINHD-1X1; 1X01
SDA: PINHD-1X1; 1X01
SOLAR1+, SOLAR1-, SOLAR2+, SOLAR2-: PINHD-1X1; 1X01
SW1: SWITCH_SPST_4_PINRECT; TACTILE_SWITCH_SMD_4.6X2.8MM
SWCLK: PINHD-1X1; 1X01
SWDIO: PINHD-1X1; 1X01
U1: MCP111T-240E/TT; SOT95P237X112-3N; MPN MCP111T-240E/TT
U2: SPX3819-3.3; SOT23-5
U5: ATSAMD21G18_QFN; TQFN48_7MM
U7: LT1634-1,25BMCMS8; MSOP8
VBUS: PINHD-1X1; 1X01
X1: 32.768; XTAL3215

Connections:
3V3SW: 3V3SW.1; also elsewhere on the board
!RESET: RST.1, SW1.1, SW1.2, U1.1 (VOUT), U5.40 (/RESET)
+3V3: 3V3.1, C5.1, C7.1, C8.1, C19.1, LED1.1 (VDD), U1.3 (VDD), U2.5 (OUT), U5.6 (VDDA), U5.17 (VDDIO), U5.36 (VDDIO), U5.44 (VDDIN); also elsewhere on the board
A0: R7.2, U5.3 (PA02/EINT2/AIN0/Y0/VOUT), U7.6 (VOUT)
A1: U5.7 (PB08/I8/AIN2/SERCOM4.0); also elsewhere on the board
A2: U5.8 (PB09/I9/AIN3/SERCOM4.1)
A3: U5.9 (PA04/EINT4/VREFB/AIN4/SERCOM0.0); also elsewhere on the board
A4: U5.10 (PA05/EINT5/AIN5/SERCOM0.1)
A5: U5.47 (PB02/I2/AIN10/SERCOM5.0); also elsewhere on the board
AREF: C14.1, U5.4 (PA03/EINT3/VREFA/AIN1)
D0: U5.16 (PA11/I11/AIN19/SERCOM0+2.3/I2SF0); also elsewhere on the board
D1: U5.15 (PA10/I10/AIN18/SERCOM0+2.2/I2SCK); also elsewhere on the board
D2: U5.23 (PA14/I14/SERCOM2+4.2); also elsewhere on the board
D3: U5.14 (PA09/I2C/I9/AIN17/SERCOM0+2.1/I2SMC)
D5: U5.24 (PA15/I15/SERCOM3+4.3); also elsewhere on the board
D6: U5.29 (PA20/I4/SERCOM3+5.2/I2SSC); also elsewhere on the board
D7: U5.30 (PA21/I5/SERCOM3+5.3/I2SFS0); also elsewhere on the board
D8: U5.11 (PA06/EINT6/AIN6/SERCOM0.2)
D9: R3.1, R6.2, U5.12 (PA07/I7/AIN7/SERCOM0.3/I2SD0)
D10: U5.27 (PA18/I2/SERCOM1+3.2); also elsewhere on the board
D11: U5.25 (PA16/I2C/I0/SERCOM1+3.0); also elsewhere on the board
D12: U5.28 (PA19/I3/SERCOM1+3.3/I2SD0); also elsewhere on the board
D13: LED1.4 (DIN), R10.1, U5.26 (PA17/I2C/I1/SERCOM1+3.1)
D+: CON1.D+, U5.34 (PA25/I13/SERCOM3+5.3/D+)
D-: CON1.D-, U5.33 (PA24/I12/SERCOM3+5.2/D-)
GND: C1.2, C2.2, C4.2, C5.2, C6.2, C7.2, C8.2, C14.2, C19.2, CON1.BASE@1 (GND), CON1.BASE@2 (GND), CON1.GND, CON1.SPRT@1 (GND), CON1.SPRT@2 (GND), CON1.SPRT@3 (GND), CON1.SPRT@4 (GND), GND2.1, GND3.1, LED1.3 (VSS), LED2.C, R6.1, SOLAR1-.1, SOLAR2-.1, SW1.3, SW1.4, U1.2 (VSS), U2.2 (GND), U5.5 (GNDA), U5.18 (GND), U5.35 (GND), U5.42 (GND), U5.THERMAL (GND), U7.4 (GND); also elsewhere on the board
MISO: MISO.1, U5.21 (PA12/I12/I2C/SERCOM2+4.0)
MOSI: MOSI.1, U5.19 (PB10/I10/SERCOM4.2/I2SMC)
unnamed: LED2.A, R10.2
unnamed: D6.A, SOLAR1+.1
unnamed: C2.1, U5.1 (PA00/EINT0/SERCOM1.0), X1.P$1
unnamed: C4.1, U5.2 (PA01/EINT1/SERCOM1.1), X1.P$2
unnamed: D5.A, SOLAR2+.1
unnamed: CON1.VBUS, D4.A
SCK: SCK.1, U5.20 (PB11/I11/SERCOM4.3/I2SCL)
SCL: SCL.1, U5.32 (PA23/I2C/I7/SERCOM3+5.1/SOF); also elsewhere on the board
SDA: SDA.1, U5.31 (PA22/I2C/I6/SERCOM3+5.0); also elsewhere on the board
SD_CS: CS.1, U5.13 (PA08/I2C/AIN16/SERCOM0+2.0/I2SD1)
SWCLK: SWCLK.1, U5.45 (PA30/I10/SECOM1.2/SWCLK)
SWDIO: SWDIO.1, U5.46 (PA31/I11/SECOM1.3/SWDIO)
VBAT: D1.A; also elsewhere on the board
VBUS: C6.1, D1.C, D4.C, D5.C, D6.C, R3.2, R7.1, U2.1 (IN), U2.3 (EN), VBUS.1; also elsewhere on the board
VDDCORE1: C1.1, U5.43 (VDDCORE)

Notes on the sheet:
POWER AND FILTERING
RESET
N/C
TXLED
USBHOSTEN
RXLED
TXD
RXD
USB
BREAKOUTS
LEDs
MICROCONTROLLER
WS2812B
SOLAR PANEL CONNECTIONS

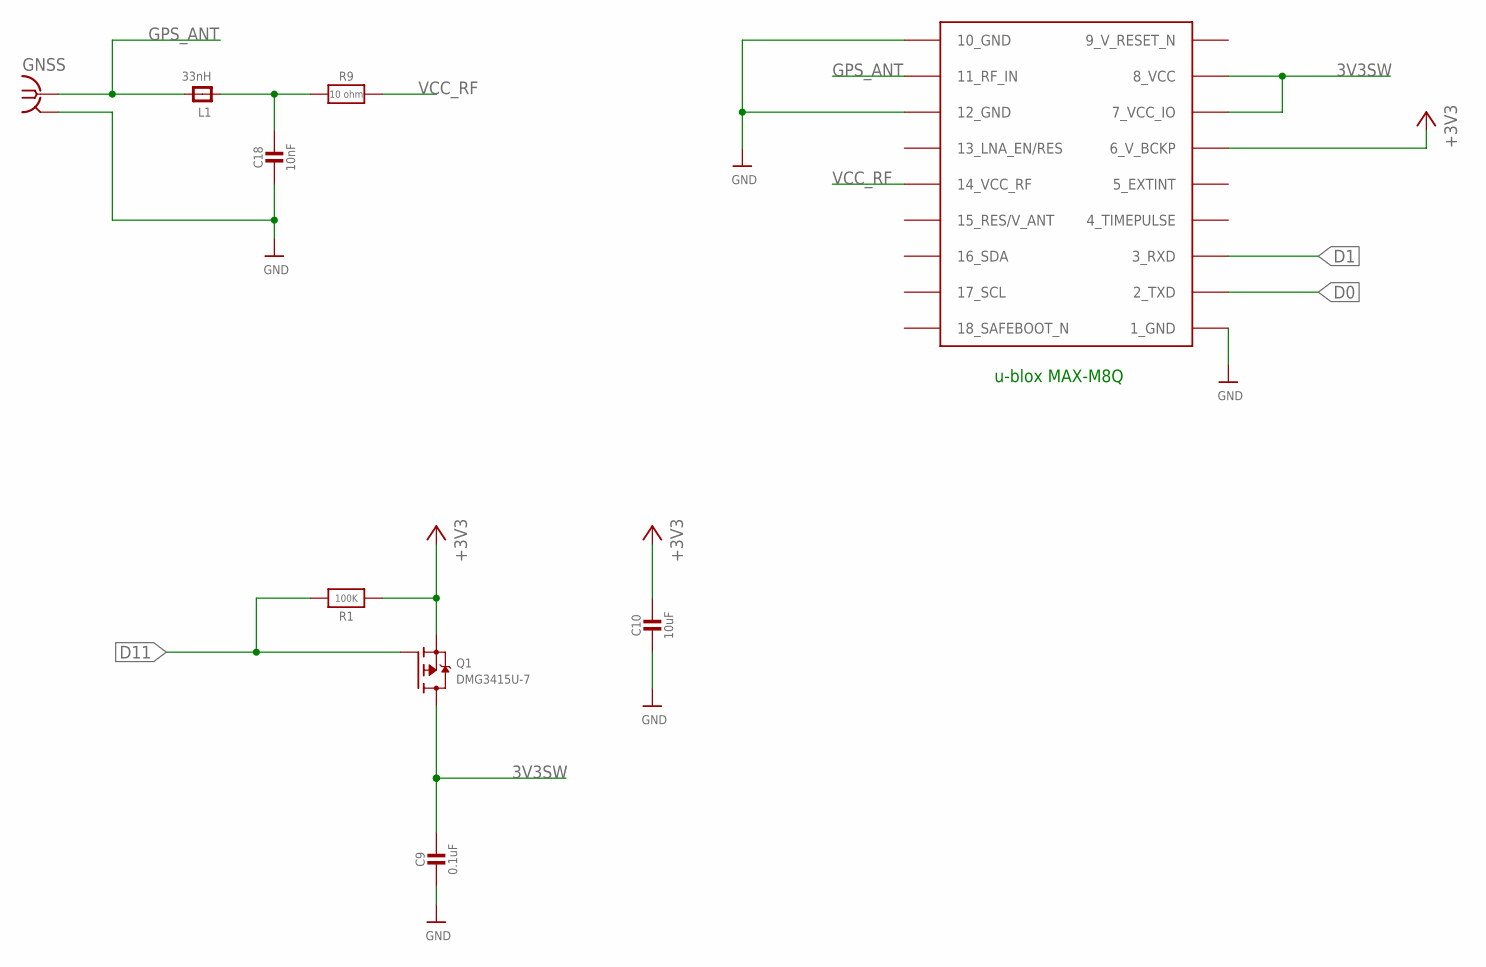
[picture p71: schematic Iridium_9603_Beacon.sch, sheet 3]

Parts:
C9: 0.1uF; 0805-NO
C10: 10uF; 0805-NO
C18: 10nF; 0805-NO
GNSS: SMA-142-0711-821/826; J502-ND-142-0711-821/826
L1: 33nH; 0805-NO
Q1: DMG3415U-7; SOT23-WIDE
R1: 100K; 0805-NO
R9: 10 ohm; 0805-NO
U6: MAX-M8

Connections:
3V3SW: C9.1, Q1.3 (D), U6.7_VCC_IO, U6.8_VCC; also elsewhere on the board
9_V_RESET_N: U6.9_RESET_N (9_V_RESET_N)
+3V3: C10.1, Q1.2 (S), R1.1, U6.6_V_BCKP; also elsewhere on the board
D0: U6.2_TXD; also elsewhere on the board
D1: U6.3_RXD; also elsewhere on the board
D11: Q1.1 (G), R1.2; also elsewhere on the board
GND: C9.2, C10.2, C18.2, GNSS.G@1 (2), GNSS.G@2 (2), GNSS.G@3 (2), GNSS.G@4 (2), U6.1_GND, U6.10_GND, U6.12_GND; also elsewhere on the board
GPS_ANT: GNSS.1, L1.2, U6.11_RF_IN
unnamed: C18.1, L1.1, R9.1
VCC_RF: R9.2, U6.14_VCC_RF

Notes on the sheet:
u-blox MAX-M8Q

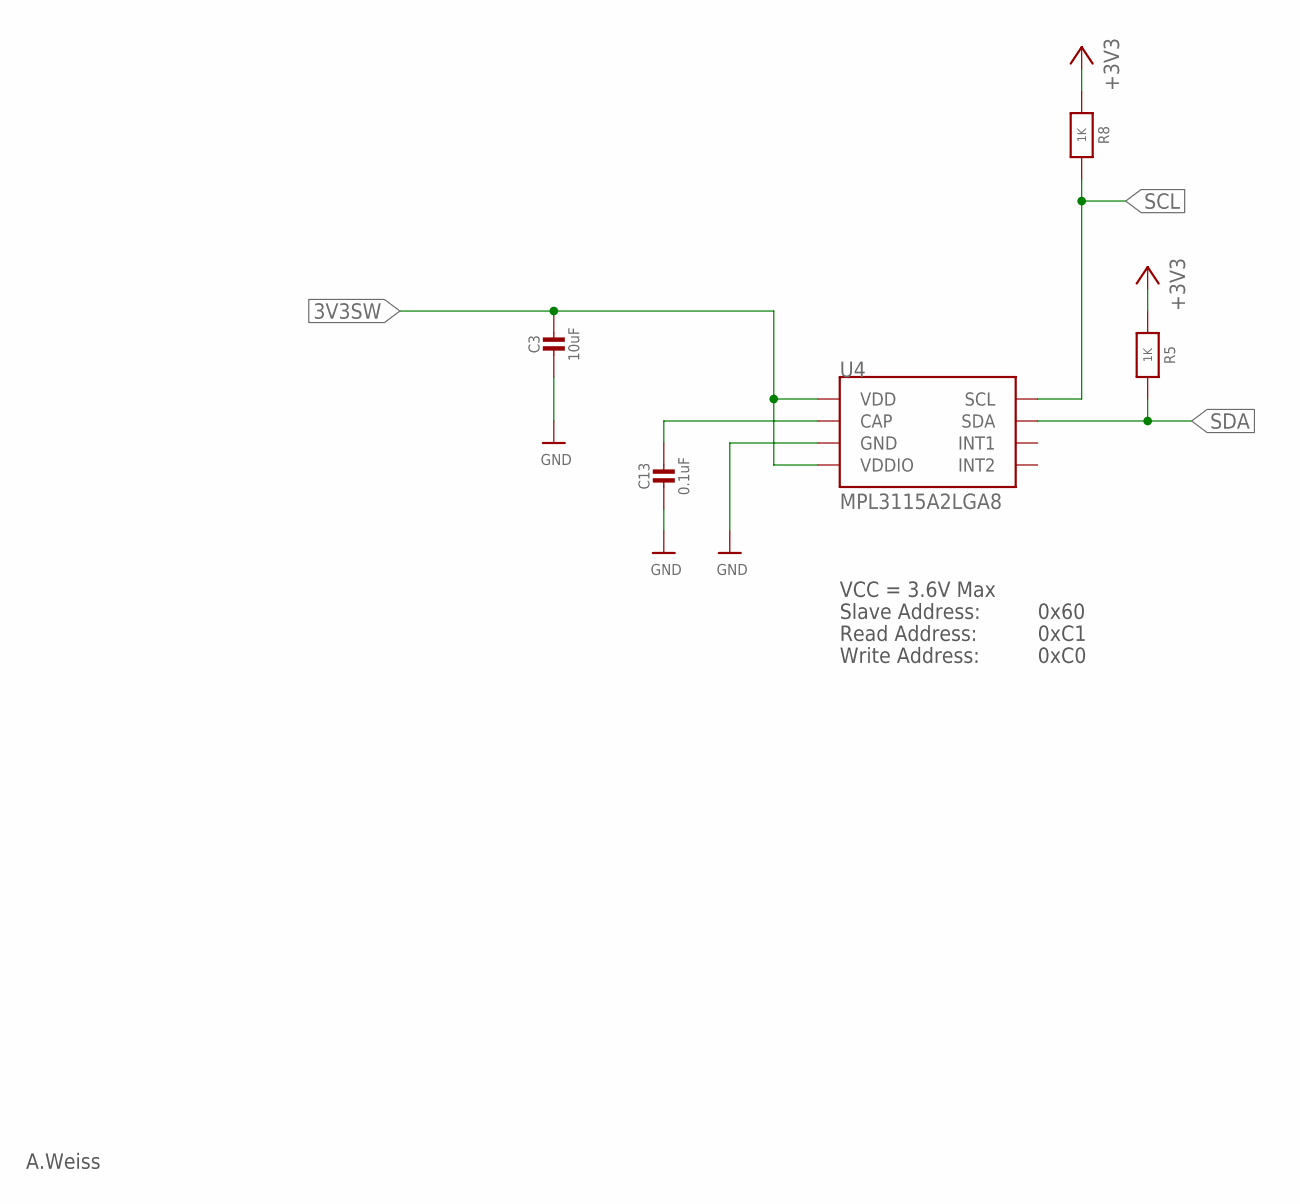
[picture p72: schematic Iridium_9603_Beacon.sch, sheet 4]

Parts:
C3: 10uF; 0805-NO
C13: 0.1uF; 0805-NO
R5, R8: 1K; 0603-NO
U4: MPL3115A2LGA8; LGA8

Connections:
3V3SW: C3.1, U4.1 (VDD), U4.4 (VDDIO); also elsewhere on the board
+3V3: R5.1, R8.1; also elsewhere on the board
GND: C3.2, C13.2, U4.3 (GND); also elsewhere on the board
unnamed: C13.1, U4.2 (CAP)
SCL: R8.2, U4.8 (SCL); also elsewhere on the board
SDA: R5.2, U4.7 (SDA); also elsewhere on the board

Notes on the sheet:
A.Weiss
VCC = 3.6V Max
Read Address:
Write Address:
Slave Address:
0x60
0xC1
0xC0

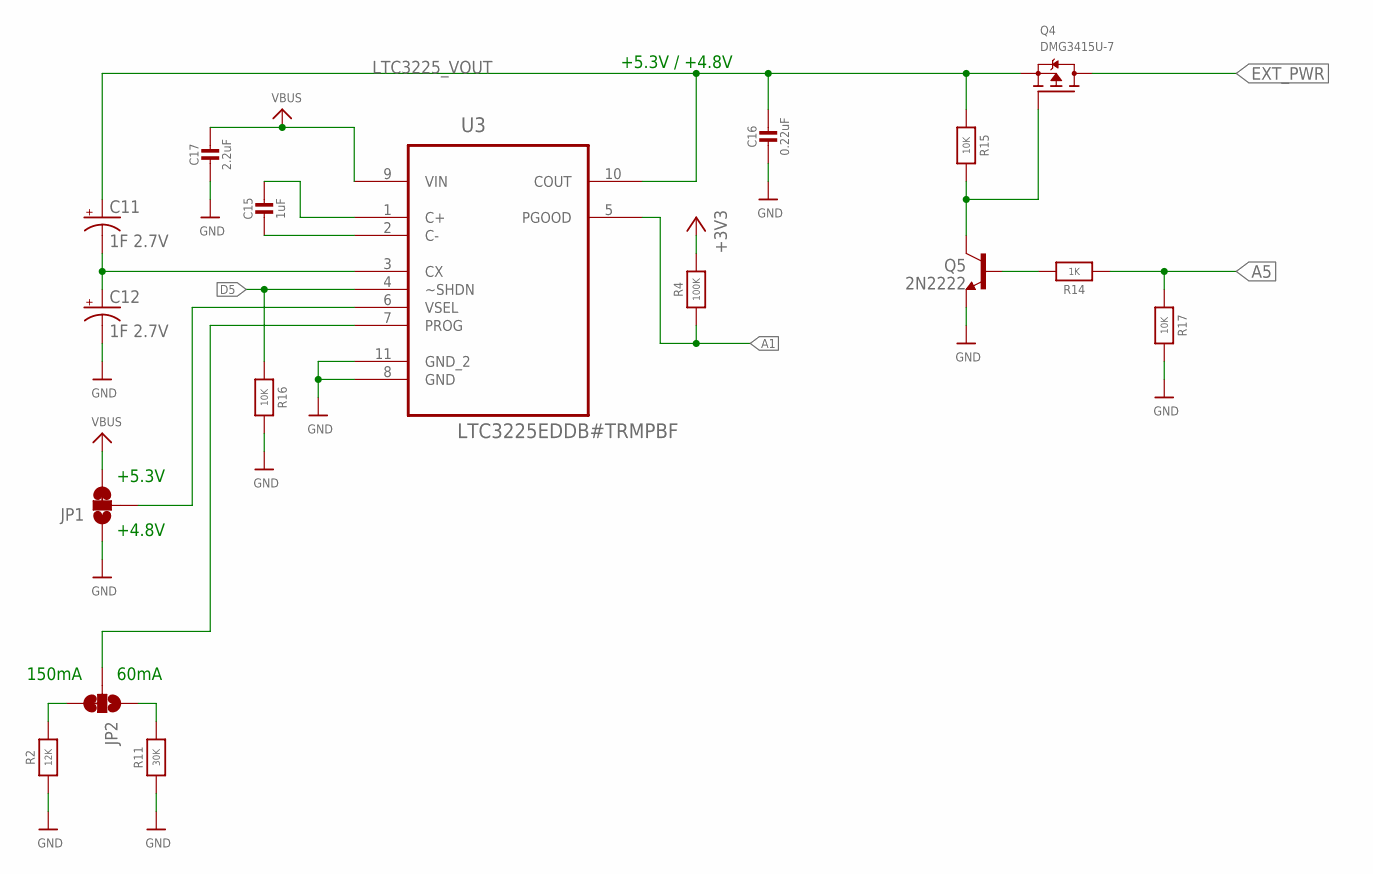
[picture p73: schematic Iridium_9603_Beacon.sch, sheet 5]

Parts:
C11, C12: 1F 2.7V; CPOL-RADIAL-1F-2.7V
C15: 1uF; 0603-NO
C16: 0.22uF; 0603-NO
C17: 2.2uF; 0805-NO
JP1, JP2: JUMPER-PAD-3-2OF3_NC_BY_TRACE_LARGE; PAD-JUMPER-3-2OF3_NC_BY_TRACE_YES_SILK_LARGE
Q4: DMG3415U-7; SOT23-WIDE
Q5: 2N2222; SOT23-BEC
R2: 12K; 0805-NO
R4: 100K; 0805-NO
R11: 30K; 0805-NO
R14: 1K; 0603-NO
R15, R16, R17: 10K; 0603-NO
U3: LTC3225EDDB#TRMPBF; DFN300X200-10L

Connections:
+3V3: R4.2; also elsewhere on the board
A1: R4.1, U3.5 (PGOOD); also elsewhere on the board
A5: R14.1, R17.1; also elsewhere on the board
D5: R16.1, U3.4 (~SHDN); also elsewhere on the board
EXT_PWR: Q4.3 (D); also elsewhere on the board
GND: C12.-, C16.2, C17.2, JP1.1, Q5.E, R2.1, R11.1, R16.2, R17.2, U3.8 (GND), U3.11 (GND_2); also elsewhere on the board
LTC3225_VOUT: C11.+, C16.1, Q4.2 (S), R15.1, U3.10 (COUT)
unnamed: C11.-, C12.+, U3.3 (CX)
unnamed: C15.2, U3.2 (C-)
unnamed: C15.1, U3.1 (C+)
unnamed: JP2.2, U3.7 (PROG)
unnamed: JP1.2, U3.6 (VSEL)
unnamed: JP2.3, R2.2
unnamed: JP2.1, R11.2
unnamed: Q4.1 (G), Q5.C, R15.2
unnamed: Q5.B, R14.2
VBUS: C17.1, JP1.3, U3.9 (VIN); also elsewhere on the board

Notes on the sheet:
+5.3V / +4.8V
+5.3V
+4.8V
150mA
60mA

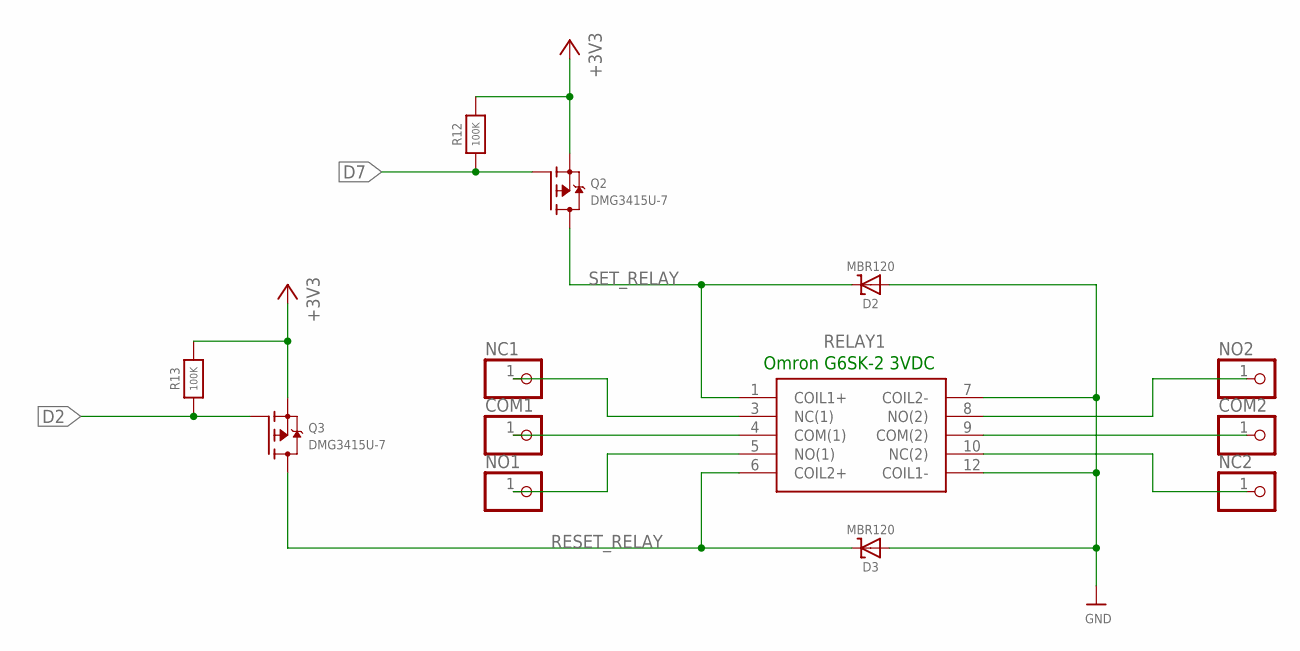
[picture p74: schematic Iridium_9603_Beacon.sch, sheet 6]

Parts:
COM1, COM2: PINHD-1X1; 1X01
D2, D3: MBR120; SOD-123
NC1, NC2: PINHD-1X1; 1X01
NO1, NO2: PINHD-1X1; 1X01
Q2, Q3: DMG3415U-7; SOT23-WIDE
R12, R13: 100K; 0805-NO
RELAY1: G6SK-2_DC5; G6SK2DC5

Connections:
+3V3: Q2.2 (S), Q3.2 (S), R12.2, R13.2; also elsewhere on the board
D2: Q3.1 (G), R13.1; also elsewhere on the board
D7: Q2.1 (G), R12.1; also elsewhere on the board
GND: D2.A, D3.A, RELAY1.7 (COIL2-), RELAY1.12 (COIL1-); also elsewhere on the board
unnamed: NC1.1, RELAY1.3 (NC(1))
unnamed: COM1.1, RELAY1.4 (COM(1))
unnamed: NO1.1, RELAY1.5 (NO(1))
unnamed: NO2.1, RELAY1.8 (NO(2))
unnamed: COM2.1, RELAY1.9 (COM(2))
unnamed: NC2.1, RELAY1.10 (NC(2))
RESET_RELAY: D3.C, Q3.3 (D), RELAY1.6 (COIL2+)
SET_RELAY: D2.C, Q2.3 (D), RELAY1.1 (COIL1+)

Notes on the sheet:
Omron G6SK-2 3VDC

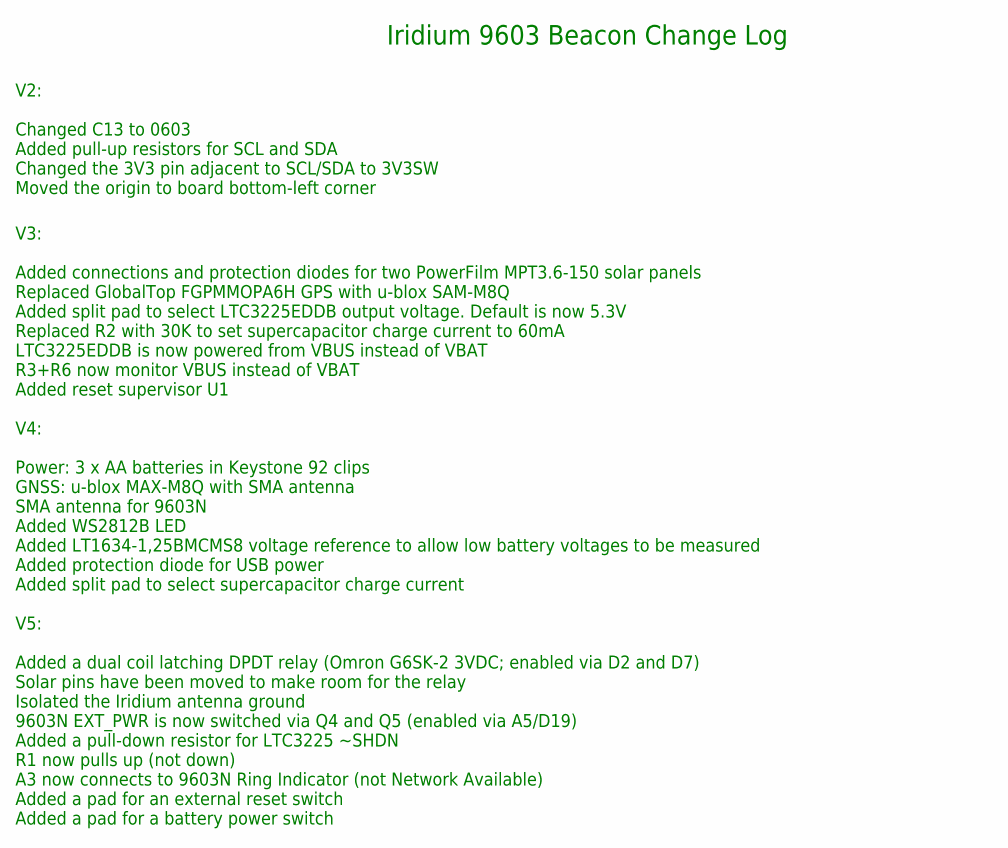
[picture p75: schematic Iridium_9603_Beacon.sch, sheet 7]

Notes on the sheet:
V2: Changed C13 to 0603 Added pull-up resistors for SCL and SDA Changed the 3V3 pin adjacent to SCL/SDA to 3V3SW Moved the origin to board bottom-left corner
Iridium 9603 Beacon Change Log
V3: Added connections and protection diodes for two PowerFilm MPT3.6-150 solar panels Replaced GlobalTop FGPMMOPA6H GPS with u-blox SAM-M8Q Added split pad to select LTC3225EDDB output voltage. Default is now 5.3V Replaced R2 with 30K to set supercapacitor charge current to 60mA LTC3225EDDB is now 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
V4: Power: 3 x AA batteries in Keystone 92 clips GNSS: u-blox MAX-M8Q with SMA antenna SMA antenna for 9603N Added WS2812B LED Added LT1634-1,25BMCMS8 voltage reference to allow low battery voltages to be measured Added protection diode for USB power Added split pad to select supercapacitor charge 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
V5: Added a dual coil latching DPDT relay (Omron G6SK-2 3VDC; enabled via D2 and D7) Solar pins have been moved to make room for the relay Isolated the Iridium antenna ground 9603N EXT_PWR is now switched via Q4 and Q5 (enabled via A5/D19) Added a pull-down resistor for LTC3225 ~SHDN R1 now pulls u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

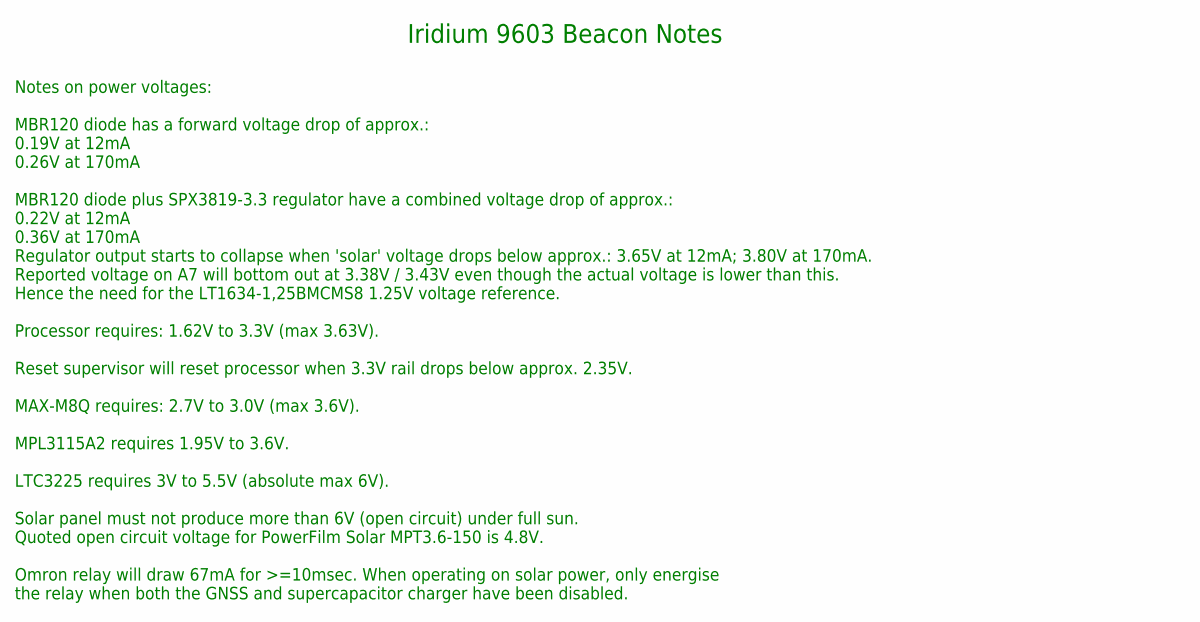
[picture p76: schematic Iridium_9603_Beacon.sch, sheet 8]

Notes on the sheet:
Iridium 9603 Beacon Notes
Notes on power voltages: MBR120 diode has a forward voltage drop of approx.: 0.19V at 12mA 0.26V at 170mA MBR120 diode plus SPX3819-3.3 regulator have a combined voltage drop of approx.: 0.22V at 12mA 0.36V at 170mA Regulator output starts to collapse when 'solar' voltage drops below approx.: 3.65V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

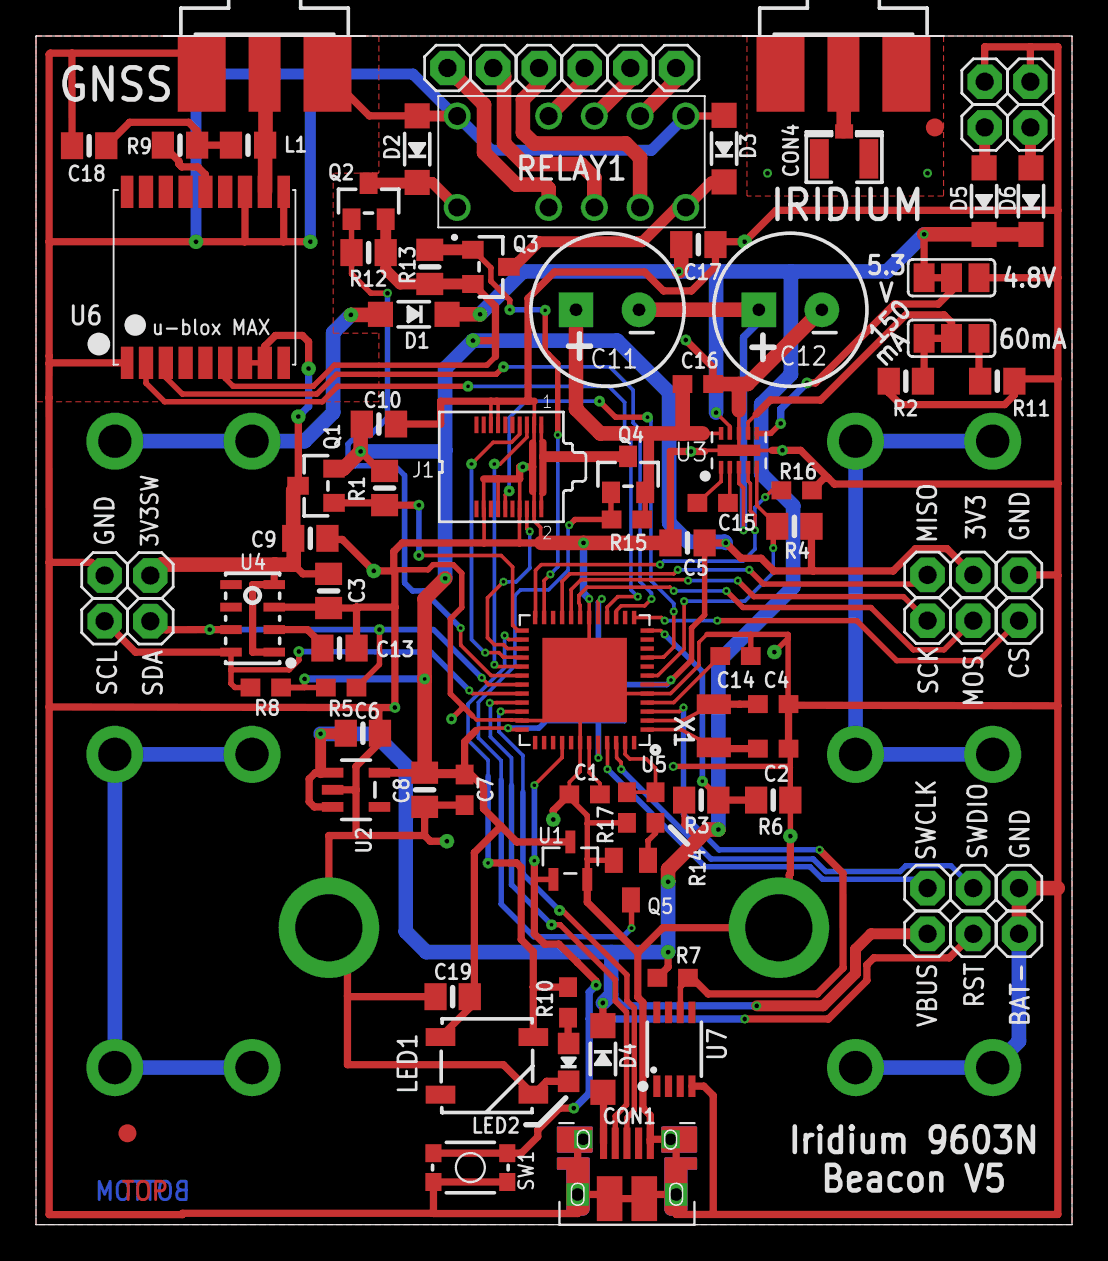
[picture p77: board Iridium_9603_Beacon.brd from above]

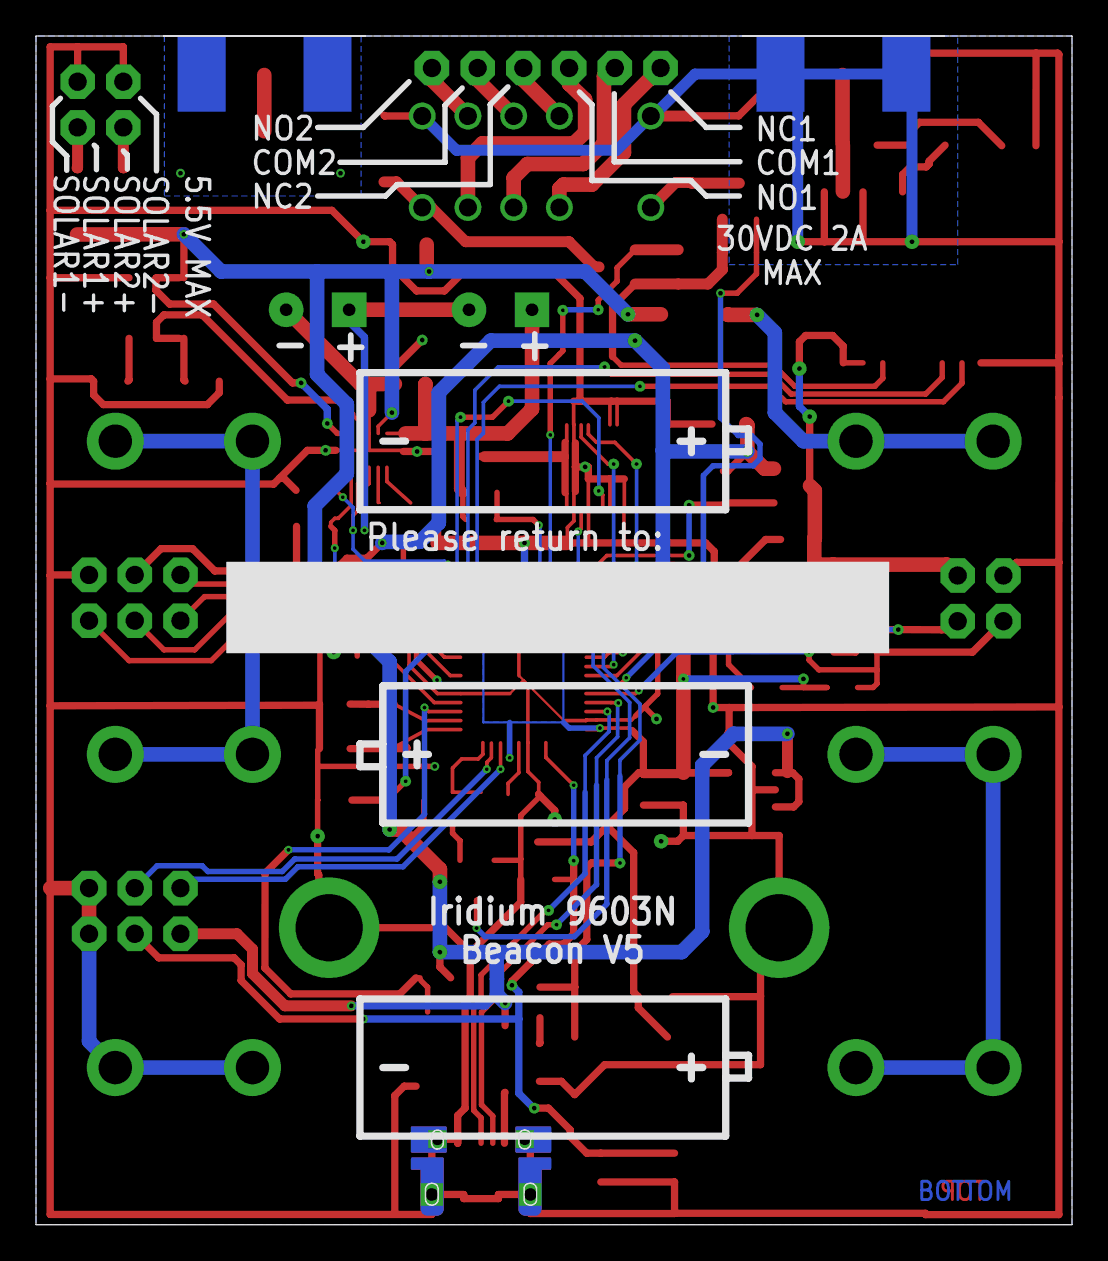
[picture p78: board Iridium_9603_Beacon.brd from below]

Board: 2 copper layers, 57.6 x 66.0 mm, 100 parts (3 on the bottom side), 67 nets.

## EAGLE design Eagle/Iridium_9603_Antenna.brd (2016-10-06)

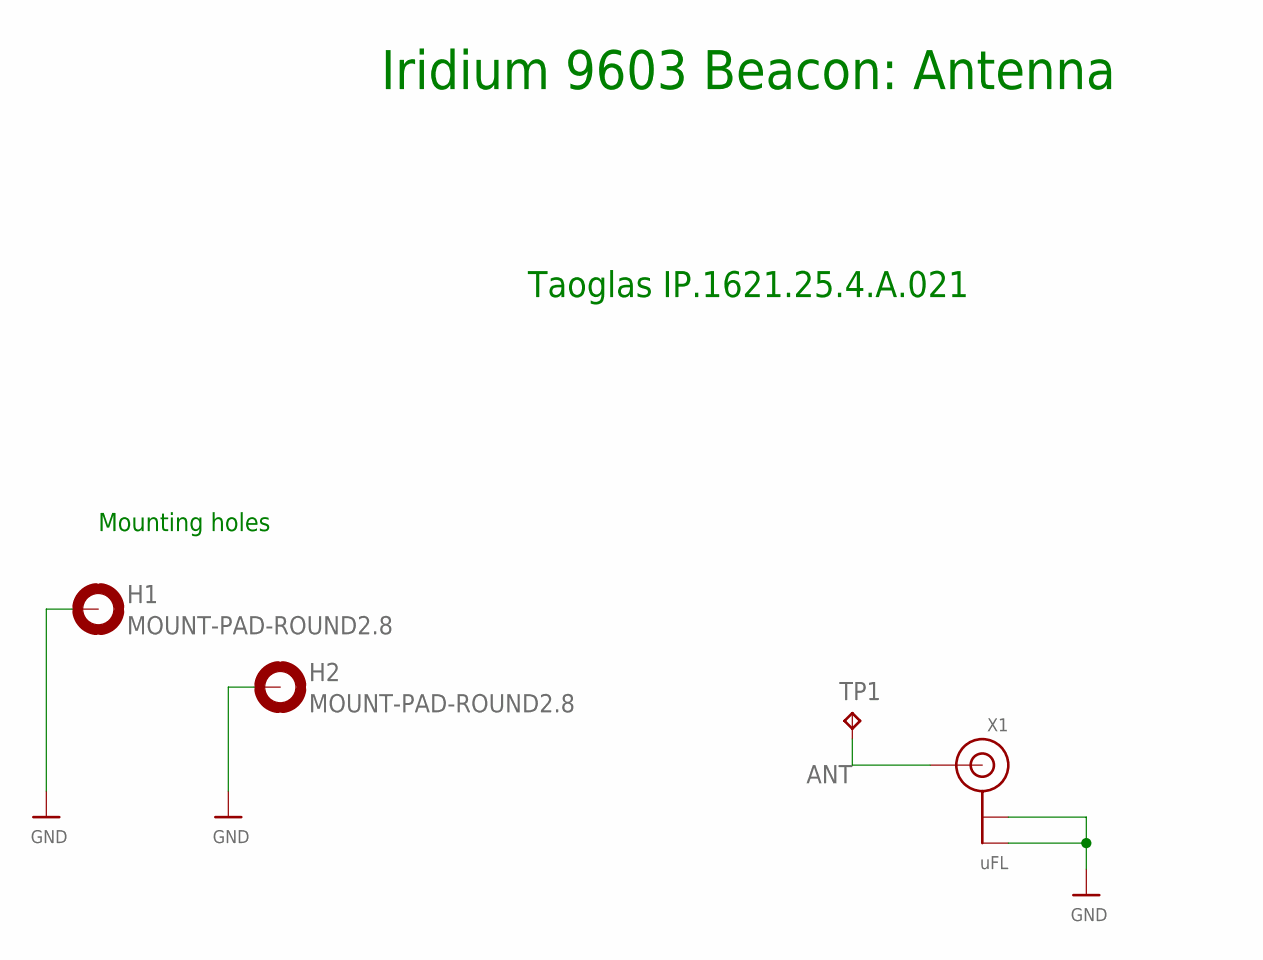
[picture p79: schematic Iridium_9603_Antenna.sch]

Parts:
H1, H2: MOUNT-PAD-ROUND2.8; 2,8-PAD
TP1: TPB2,54; B2,54
X1: uFL; U.FL

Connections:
ANT: TP1.TP, X1.3 (SIGNAL)
GND: H1.B2,8, H2.B2,8, X1.1 (GND), X1.2 (GND)

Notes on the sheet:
Mounting holes
Iridium 9603 Beacon: Antenna
Taoglas IP.1621.25.4.A.021

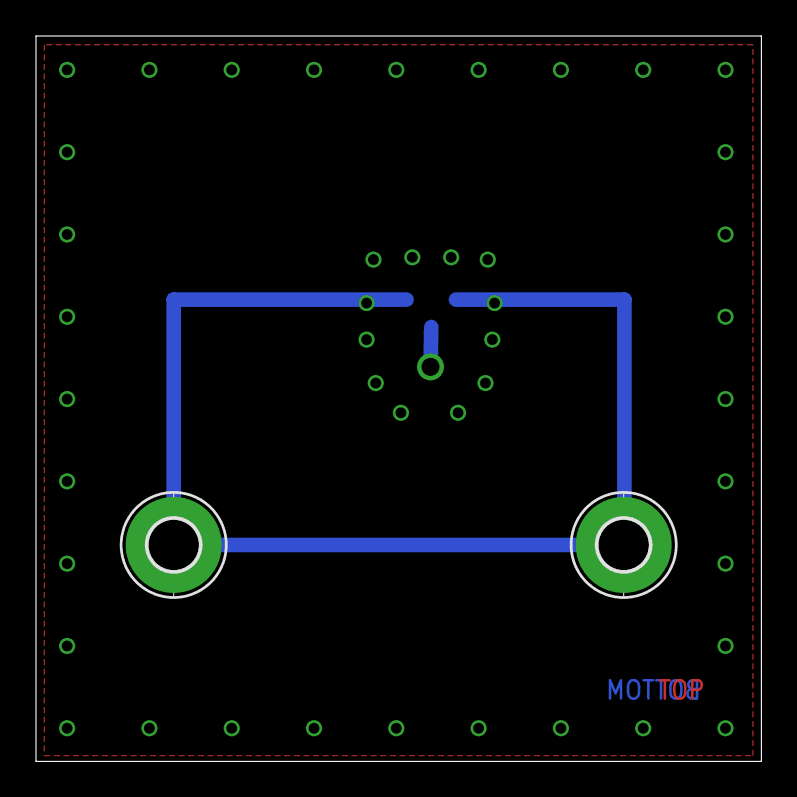
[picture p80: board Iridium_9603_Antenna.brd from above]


Board: 2 copper layers, 40.3 x 40.3 mm, 4 parts (2 on the bottom side), 2 nets.

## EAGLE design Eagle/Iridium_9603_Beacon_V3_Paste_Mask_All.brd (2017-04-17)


Board: 2 copper layers, 50.8 x 81.3 mm, 40 parts (0 on the bottom side), 2 nets, no tracks yet.

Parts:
C1, C7, C14, C15: 1uF; 0603-NO
C2, C4: 22pF; 0603-NO
C3, C5, C10: 10uF; 0805-NO
C6, C8: 10µF; 0805-NO
C9: 0.1uF; 0805-NO
C13: 0.1uF; 0603-NO
C16: 0.22uF; 0603-NO
C17: 2.2uF; 0805-NO
CON1: FCI_10103594
D1, D2, D3: MBR120; SOD-123
FD3, FD4: FIDUCIAL; FIDUCIAL-1X2-111%
J1: SS4-10-3.50-X-D
LED1: RED; CHIPLED_0805_NOOUTLINE
Q1: DMG3415U-7; SOT23-WIDE
R1, R4: 100K; 0805-NO
R2: 30K; 0805-NO
R3: 100k; 0603-NO
R5, R8: 1K; 0603-NO
R6: 100K; 0603-NO
R7: 2.2K; 0603-NO
SW1: TACTILE_SWITCH_SMD_4.6X2.8MM
U1: MCP111T-195I/TT; SOT95P237X112-3N
U2: SPX3819-3.3; SOT23-5
U3: LTC3225EDDB#TRMPBF; DFN300X200-10L
U4: MPL3115A2LGA8; LGA8
U5: ATSAMD21G18_QFN; TQFN48_7MM
U6: SAM-M8Q
X1: 32.768; XTAL3215

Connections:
GND: C16.2, CON1.BASE@1, CON1.BASE@2, CON1.GND, CON1.SPRT@1, CON1.SPRT@2, CON1.SPRT@3, CON1.SPRT@4, U2.2, U5.18, U5.35, U5.42, U5.THERMAL
VDDIO: U5.17, U5.36

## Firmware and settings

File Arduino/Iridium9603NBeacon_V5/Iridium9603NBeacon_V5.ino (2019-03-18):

// ###########################
// # Iridium 9603N Beacon V5 #
// ###########################

// This version provides support for the Iridium Beacon Radio Board based on the LPRS eRIC4/9
// eRIC Pin4 Tx (input) is connected to MOSI (Digital Pin 23, Port B Pin 10, SERCOM4 Pad 2, Serial3 Tx)
// eRIC Pin3 Rx (output) is connected to SCK (Digital Pin 24, Port B Pin 11, SERCOM4 Pad 3, Serial3 Rx)
// eRIC Pin2 CTS / BUSY (output) is connected to MISO (Digital Pin 22)
// eRIC Pin22 (wake from low power) is connected to CS (Digital Pin 4)
// The radio board is optional - the code will work the same with or without it
// The message to be transmitted by the radio board should be sent in an Iridium Mobile Terminated message
// (e.g. from RockBLOCK Operations or a Beacon Base) containing [RADIO=nnnnnnnn] where "nnnnnnnn" is
// the radio message (usually the serial number of the eRIC on a Pyro Cut-Down)

// Stores both source and destination RockBLOCK serial numbers in flash.
// The default values are:
#define RB_destination 0 // Serial number of the destination RockBLOCK (int). Set to zero to disable RockBLOCK message forwarding
#define RB_source 0 // Serial number of this unit (int)

// Updated for the V5 PCB: provides support for an OMRON G6SK relay; 9603N EXT_PWR is switched via a P-MOSFET.

// OMRON G6SK relay:
// Set coil is connected to D7 (pull low to energise the relay coil)
// Reset coil is connected to D2 (pull low to energise the relay coil)
// The relay can be set/reset via an Iridium Mobile Terminated message (e.g. from RockBLOCK Operations or a Beacon Base) containing
// [RELAY=ON] or [RELAY=OFF]
// The relay can also be pulsed on (set) for 1-5 seconds via MT message containing
// [RELAY=1] or [RELAY=2] or [RELAY=3] or [RELAY=4] or [RELAY=5]

// Power for the 9603N is switched by a DMG3415 P-channel MOSFET
// A 2N2222 NPN transistor pulls the MOSFET gate low
// A high on A5 (D19) enables power to the 9603N

// Uses Cristian Maglie's FlashStorage library to store the BEACON_INTERVAL setting
// https://github.com/cmaglie/FlashStorage
// BEACON_INTERVAL can be updated via an Iridium Mobile Terminated message (e.g. from RockBLOCK Operations or a Beacon Base)

// Power can be provided by: two PowerFilm MPT3.6-150 solar panels; USB; 3 x Energiser Ultimate Lithium AA batteries
// GNSS data is provided by u-blox MAX-M8Q
// WB2812B NeoPixel is connected to D13 in parallel with a standard Red LED (for the bootloader)
// 1.25V precision voltage reference is connected to A0 to allow lower battery voltages to be measured

// With grateful thanks to Mikal Hart:
// Based on Mikal's IridiumSBD Beacon example: https://github.com/mikalhart/IridiumSBD
// Requires Mikal's TinyGPS library: https://github.com/mikalhart/TinyGPS
// and PString: http://arduiniana.org/libraries/pstring/

// With grateful thanks to:
// Adafruit: https://learn.adafruit.com/using-atsamd21-sercom-to-add-more-spi-i2c-serial-ports/creating-a-new-serial
// MartinL: https://forum.arduino.cc/index.php?topic=341054.msg2443086#msg2443086

// The Iridium_9603_Beacon PCB is based extensively on the Adafruit Feather M0 (Adalogger)
// https://www.adafruit.com/products/2796
// GPS data provided by u-blox MAX-M8Q
// https://www.u-blox.com/en/product/max-m8-series
// Pressure (altitude) and temperature provided by MPL3115A2
// Requires Adafruit's MPL3115A2 library
// https://github.com/adafruit/Adafruit_MPL3115A2_Library

// Support for the WB2812B is provided by Adafruit:
// https://github.com/adafruit/Adafruit_NeoPixel

// Uses RTCZero to provide sleep functionality (on the M0)
// https://github.com/arduino-libraries/RTCZero

// With grateful thanks to CaveMoa for his SimpleSleepUSB example
// https://github.com/cavemoa/Feather-M0-Adalogger
// https://github.com/cavemoa/Feather-M0-Adalogger/tree/master/SimpleSleepUSB
// Note: you will need to close and re-open your serial monitor each time the M0 wakes up

// With thanks to David A. Mellis and Tom Igoe for the smoothing tutorial
// http://www.arduino.cc/en/Tutorial/Smoothing

// Iridium 9603N is interfaced to M0 using Serial2
// D6 (Port A Pin 20) = Enable (Sleep) : Connect to 9603 ON/OFF Pin 5
// D10 (Port A Pin 18) = Serial2 TX : Connect to 9603 Pin 6
// D12 (Port A Pin 19) = Serial2 RX : Connect to 9603 Pin 7
// A3 / D17 (Port A Pin 4) = Ring Indicator : Connect to 9603 Pin 12

// Power to the 9603N is switched by a P-channel MOSFET
// The MOSFET gate is pulled high by a 10K resistor. The gate is pulled low by a 2N2222 NPN transistor
// Power is enabled by pulling the base of the transistor high
// The transistor base is connected to A5 / D19 (Port B Pin 2)

// Iridium 9603 is powered from Linear Technology LTC3225 SuperCapacitor Charger
// (fitted with 2 x 10F 2.7V caps e.g. Bussmann HV1030-2R7106-R)
// (or 2 x 1F 2.7V caps e.g. Bussmann HV0810-2R7105-R)
// to provide the 1.3A peak current when the 9603 is transmitting.
// Charging 10F capacitors to 5.3V at 60mA could take ~7 minutes!
// (~6.5 mins to PGOOD, ~7 mins to full charge)
// 1F capacitors charge in approx. 1/10 of that time.
// Setting the charging current to 150mA will reduce the time further.
// 5.3V is OK as the 9603N has an extended supply voltage range of +5 V +/- 0.5 V
// http://www.linear.com/product/LTC3225
// D5 (Port A Pin 15) = LTC3225 ~Shutdown
// A1 / D15 (Port B Pin 8) = LTC3225 PGOOD

// MAX-M8Q GNSS is interfaced to M0 using Serial1
// D1 (Port A Pin 10) = Serial1 TX : Connect to GPS RX
// D0 (Port A Pin 11) = Serial1 RX : Connect to GPS TX
// D11 (Port A Pin 16) = GPS ENable : Connect to GPS EN(ABLE)

// MPL3115A2 Pressure (Altitude) and Temperature Sensor
// D20 (Port A Pin 22) = SDA : Connect to MPL3115A2 SDA
// D21 (Port A Pin 23) = SCL : Connect to MPL3115A2 SCL

// D13 (Port A Pin 17) = WB2812B NeoPixel + single Red LED
// D9 (Port A Pin 7) = AIN 7 : Bus Voltage / 2
// D14 (Port A Pin 2) = AIN 0 : 1.25V precision voltage reference

// D7 (Port A Pin 21) = OMRON relay set coil (pull low to energise the coil via a P-channel MOSFET)
// D2 (Port A Pin 14) = OMRON relay reset coil (pull low to energise the coil via a P-channel MOSFET)

// As the solar panel or battery voltage drops, reported VBUS on A7 drops to ~3.4V and then flatlines
// as the 3.3V rail starts to collapse. The 1.25V reference on A0 allows lower voltages to be measured
// as the signal on A0 will appear to _rise_ as the 3.3V rail collapses.

// Red LED on D13 shows when the SAMD is in bootloader mode (LED will fade up/down)

// WB2812B on D13 indicates what the software is doing:
// Magenta at power up (loop_step == init) (~10 seconds)
// Blue when waiting for a GNSS fix (loop_step == start_GPS or read_GPS or read_pressure) (could take 5 mins)
// Cyan when waiting for supercapacitors to charge (loop_step == start_LTC3225 or wait_LTC3225) (could take 7 mins)
// White during Iridium transmit (loop_step == start_9603) (could take 5 mins)
// Green flash (2 seconds) indicates successful transmission
// Red flash (2+ seconds) entering sleep
// LED will flash Red after: Iridium transmission (successful or failure); low battery detected; no GNSS data; supercapacitors failed to charge
// WB2812B blue LED has the highest forward voltage and is slightly dim at 3.3V. The red and green values are adapted accordingly (222 instead of 255).

// If you bought your 9603N from Rock7, you can have your messages delivered to another RockBLOCK automatically:
// https://www.rock7.com/shop-product-detail?productId=50
// http://www.rock7mobile.com/products-rockblock-9603
// http://www.rock7mobile.com/downloads/RockBLOCK-9603-Developers-Guide.pdf (see last page)
// Change RB_destination (above) to the serial number of the destination RockBLOCK
// Change RB_source (above) to the serial number of this RockBLOCK
// Both RBSOURCE and RBDESTINATION can be updated via a MT message.
// Note: the RockBLOCK gateway does not remove the destination RockBLOCK address from the SBD message
// so, in this code, it is included as a full CSV field

#include <IridiumSBD.h> // Requires V2: https://github.com/mikalhart/IridiumSBD
#include <TinyGPS.h> // NMEA parsing: http://arduiniana.org
#include <PString.h> // String buffer formatting: http://arduiniana.org

#include <Adafruit_NeoPixel.h> // Support for the WB2812B

#include <RTCZero.h> // M0 Real Time Clock
RTCZero rtc; // Create an rtc object

// Define how often messages are sent in MINUTES (max 1440)
// This is the _quickest_ messages will be sent. Could be much slower than this depending on:
// capacitor charge time; gnss fix time; Iridium timeout; etc.
// The default value will be overwritten with the one stored in Flash - if one exists
// The value can be changed via a Mobile Terminated message
int BEACON_INTERVAL = 5;

// Flash Storage
#include <FlashStorage.h>
typedef struct { // Define a struct to hold the flash variable(s)
  int PREFIX; // Flash storage prefix (0xB5); used to test if flash has been written to before 
  int INTERVAL; // Message interval in minutes
  // RockBLOCK source serial number: stored as an int; i.e. the RockBLOCK serial number of the 9603N attached to this beacon
  int RBSOURCE; 
  // RockBLOCK destination serial number: stored as an int; i.e. the RockBLOCK serial number of the 9603N you would like the messages delivered _to_
  int RBDESTINATION; // Set this to zero to disable RockBLOCK gateway message forwarding
  int CSUM; // Flash storage checksum; the modulo-256 sum of PREFIX and INTERVAL; used to check flash data integrity
} FlashVarsStruct;
FlashStorage(flashVarsMem, FlashVarsStruct); // Reserve memory for the flash variables
FlashVarsStruct flashVars; // Define the global to hold the variables
int RBSOURCE = RB_source;
int RBDESTINATION = RB_destination;

// MPL3115A2
#include <Wire.h>
#include <Adafruit_MPL3115A2.h>
Adafruit_MPL3115A2 baro = Adafruit_MPL3115A2();

// Serial2 pin and pad definitions (in Arduino files Variant.h & Variant.cpp)
#define PIN_SERIAL2_RX       (34ul)               // Pin description number for PIO_SERCOM on D12
#define PIN_SERIAL2_TX       (36ul)               // Pin description number for PIO_SERCOM on D10
#define PAD_SERIAL2_TX       (UART_TX_PAD_2)      // SERCOM pad 2 (SC1PAD2)
#define PAD_SERIAL2_RX       (SERCOM_RX_PAD_3)    // SERCOM pad 3 (SC1PAD3)
// Instantiate the Serial2 class
Uart Serial2(&sercom1, PIN_SERIAL2_RX, PIN_SERIAL2_TX, PAD_SERIAL2_RX, PAD_SERIAL2_TX);
HardwareSerial &ssIridium(Serial2);

// Serial3 pin and pad definitions (in Arduino files Variant.h & Variant.cpp)
// eRIC Tx (input) is connected to MOSI (Digital Pin 23, Port B Pin 10, SERCOM4 Pad 2, Serial3 Tx)
// eRIC Rx (output) is connected to SCK (Digital Pin 24, Port B Pin 11, SERCOM4 Pad 3, Serial3 Rx)
#define PIN_SERIAL3_RX       (24ul)               // Pin description number for PIO_SERCOM on D24
#define PIN_SERIAL3_TX       (23ul)               // Pin description number for PIO_SERCOM on D23
#define PAD_SERIAL3_TX       (UART_TX_PAD_2)      // SERCOM4 Pad 2 (SC4PAD2)
#define PAD_SERIAL3_RX       (SERCOM_RX_PAD_3)    // SERCOM4 Pad 3 (SC4PAD3)
// Instantiate the Serial3 class
Uart Serial3(&sercom4, PIN_SERIAL3_RX, PIN_SERIAL3_TX, PAD_SERIAL3_RX, PAD_SERIAL3_TX);
HardwareSerial &sseRIC(Serial3);

#define ssGPS Serial1 // Use M0 Serial1 to interface to the MAX-M8Q

// Leave the "#define GALILEO" uncommented to use: GPS + Galileo + GLONASS + SBAS
// Comment the "#define GALILEO" out to use the default u-blox M8 GNSS: GPS + SBAS + QZSS + GLONASS
#define GALILEO

// Set Nav Mode to Portable
static const uint8_t setNavPortable[] = {
  0xB5, 0x62, 0x06, 0x24, 0x24, 0x00, 0xFF, 0xFF, 0x00, 0x03, 0x00, 0x00, 0x00, 0x00, 0x10, 0x27, 0x00, 0x00, 
  0x05, 0x00, 0xFA, 0x00, 0xFA, 0x00, 0x64, 0x00, 0x2C, 0x01, 0x00, 0x00, 0x00, 0x00, 0x00, 0x00, 0x00, 0x00, 
  0x00, 0x00, 0x00, 0x00, 0x00, 0x00 };

// Set Nav Mode to Pedestrian
static const uint8_t setNavPedestrian[] = {
  0xB5, 0x62, 0x06, 0x24, 0x24, 0x00, 0xFF, 0xFF, 0x03, 0x03, 0x00, 0x00, 0x00, 0x00, 0x10, 0x27, 0x00, 0x00, 
  0x05, 0x00, 0xFA, 0x00, 0xFA, 0x00, 0x64, 0x00, 0x2C, 0x01, 0x00, 0x00, 0x00, 0x00, 0x00, 0x00, 0x00, 0x00, 
  0x00, 0x00, 0x00, 0x00, 0x00, 0x00 };

// Set Nav Mode to Automotive
static const uint8_t setNavAutomotive[] = {
  0xB5, 0x62, 0x06, 0x24, 0x24, 0x00, 0xFF, 0xFF, 0x04, 0x03, 0x00, 0x00, 0x00, 0x00, 0x10, 0x27, 0x00, 0x00, 
  0x05, 0x00, 0xFA, 0x00, 0xFA, 0x00, 0x64, 0x00, 0x2C, 0x01, 0x00, 0x00, 0x00, 0x00, 0x00, 0x00, 0x00, 0x00, 
  0x00, 0x00, 0x00, 0x00, 0x00, 0x00 };

// Set Nav Mode to Sea
static const uint8_t setNavSea[] = {
  0xB5, 0x62, 0x06, 0x24, 0x24, 0x00, 0xFF, 0xFF, 0x05, 0x03, 0x00, 0x00, 0x00, 0x00, 0x10, 0x27, 0x00, 0x00, 
  0x05, 0x00, 0xFA, 0x00, 0xFA, 0x00, 0x64, 0x00, 0x2C, 0x01, 0x00, 0x00, 0x00, 0x00, 0x00, 0x00, 0x00, 0x00, 
  0x00, 0x00, 0x00, 0x00, 0x00, 0x00 };

// Set Nav Mode to Airborne <1G
static const uint8_t setNavAir[] = {
  0xB5, 0x62, 0x06, 0x24, 0x24, 0x00, 0xFF, 0xFF, 0x06, 0x03, 0x00, 0x00, 0x00, 0x00, 0x10, 0x27, 0x00, 0x00, 
  0x05, 0x00, 0xFA, 0x00, 0xFA, 0x00, 0x64, 0x00, 0x2C, 0x01, 0x00, 0x00, 0x00, 0x00, 0x00, 0x00, 0x00, 0x00, 
  0x00, 0x00, 0x00, 0x00, 0x00, 0x00 };

static const int len_setNav = 42;
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
void loop()
{
  unsigned long loopStartTime = millis();

  switch(loop_step) {

    case init:

#ifndef NoLED
      LED_magenta(); // Set LED to Magenta
#endif

      // Start the serial console
      Serial.begin(115200);
      delay(10000); // Wait 10 secs - allow time for user to open serial monitor
    
      // Send welcome message
      Serial.println("Iridium 9603N Beacon V5");

      // Echo the BEACON_INTERVAL
      Serial.print("Using a BEACON_INTERVAL of ");
      Serial.print(BEACON_INTERVAL);
      Serial.println(" minutes");
      
      // Echo RBDESTINATION and RBSOURCE
      Serial.print("Using an RBDESTINATION of ");
      Serial.println(RBDESTINATION);
      Serial.print("Using an RBSOURCE of ");
      Serial.println(RBSOURCE);

      // Setup the IridiumSBD
      // (attachConsole and attachDiags methods have been replaced with ISBDConsoleCallback and ISBDDiagsCallback)
      isbd.setPowerProfile(IridiumSBD::USB_POWER_PROFILE); // Change power profile to "low current"
      isbd.useMSSTMWorkaround(false); // Redundant?

      // Check battery voltage
      // If voltage is low, go to sleep
      init_vbat(); // Use init_vbat to make sure the current true smoothed voltage is used (after coming out of deep sleep)
      if (vbat < VBAT_LOW) {
        Serial.print("***!!! LOW VOLTAGE (init) ");
        Serial.print(vbat,2);
        Serial.println(" !!!***");
        loop_step = zzz;
      }
      else {
        loop_step = start_GPS;
      }
      
      break;
      
    case start_GPS:

#ifndef NoLED
      LED_blue(); // Set LED to Blue
#endif
    
      // Power up the GPS and MPL3115A2
      Serial.println("Powering up the GPS and MPL3115A2...");
      digitalWrite(GPS_EN, GPS_ON); // Enable the GPS and MPL3115A2

      delay(2000); // Allow time for both to start
    
      // Check battery voltage now we are drawing current for the GPS
      // If voltage is low, go to sleep
      init_vbat(); // Use init_vbat to make sure the true smoothed voltage is used
      if (vbat < VBAT_LOW) {
        Serial.print("***!!! LOW VOLTAGE (start_GPS) ");
        Serial.print(vbat,2);
        Serial.println("V !!!***");
        loop_step = zzz;
      }
      else {
        loop_step = read_GPS;
      }
      
      break;

    case read_GPS:
      // Start the GPS serial port
      ssGPS.begin(9600);

      delay(1000); // Allow time for the port to open

      // Configure GPS
      Serial.println("Configuring GPS...");

      // Disable all messages except GGA and RMC
      ssGPS.println("$PUBX,40,GLL,0,0,0,0*5C"); // Disable GLL
      delay(1100);
      ssGPS.println("$PUBX,40,ZDA,0,0,0,0*44"); // Disable ZDA
      delay(1100);
      ssGPS.println("$PUBX,40,VTG,0,0,0,0*5E"); // Disable VTG
      delay(1100);
      ssGPS.println("$PUBX,40,GSV,0,0,0,0*59"); // Disable GSV
      delay(1100);
      ssGPS.println("$PUBX,40,GSA,0,0,0,0*4E"); // Disable GSA
      delay(1100);
      
      //sendUBX(setNavPortable, len_setNav); // Set Portable Navigation Mode
      //sendUBX(setNavPedestrian, len_setNav); // Set Pedestrian Navigation Mode
      //sendUBX(setNavAutomotive, len_setNav); // Set Automotive Navigation Mode
      //sendUBX(setNavSea, len_setNav); // Set Sea Navigation Mode
      sendUBX(setNavAir, len_setNav); // Set Airborne <1G Navigation Mode
      delay(1100);

      sendUBX(setNMEA, len_setNMEA); // Set NMEA: to always output COG; and set main talker to GP (instead of GN)
      delay(1100);

#ifdef GALILEO
      sendUBX(setGNSS, len_setGNSS); // Set GNSS - causes M8 to restart!
      delay(3000); // Wait an extra time for GNSS to restart
#endif

      while(ssGPS.available()){ssGPS.read();} // Flush RX buffer so we don't confuse TinyGPS with UBX acknowledgements

      // Reset TinyGPS and begin listening to the GPS
      Serial.println("Beginning to listen for GPS traffic...");
      fixFound = false; // Reset fixFound
      charsSeen = false; // Reset charsSeen
      tinygps = TinyGPS();
      
      // Look for GPS signal for up to 5 minutes
      for (tnow = millis(); !fixFound && millis() - tnow < 5UL * 60UL * 1000UL;)
      {
        if (ssGPS.available())
        {
          charsSeen = true;
          if (tinygps.encode(ssGPS.read()))
          {
            tinygps.f_get_position(&latitude, &longitude, &locationFix);
            tinygps.crack_datetime(&year, &month, &day, &hour, &minute, &second, &hundredths, &dateFix);
            altitude = tinygps.altitude(); // Altitude in cm (long) - checks that we have received a GGA message
            speed = tinygps.f_speed_mps(); // Get speed - checks that we have received an RMC message
            satellites = tinygps.satellites(); // Get number of satellites
            course = tinygps.course(); // Get course over ground
            hdop = tinygps.hdop(); // Get horizontal dilution of precision
            fixFound = locationFix != TinyGPS::GPS_INVALID_FIX_TIME && 
                       dateFix != TinyGPS::GPS_INVALID_FIX_TIME && 
                       altitude != TinyGPS::GPS_INVALID_ALTITUDE &&
                       speed != TinyGPS::GPS_INVALID_F_SPEED &&
                       satellites != TinyGPS::GPS_INVALID_SATELLITES &&
                       course != TinyGPS::GPS_INVALID_ANGLE &&
                       hdop != TinyGPS::GPS_INVALID_HDOP &&
                       year != 2000;
          }
        }

        // if we haven't seen any GPS data in 10 seconds, then stop waiting
        if (!charsSeen && millis() - tnow > 10000) {
          break;
        }

        // Check battery voltage now we are drawing current for the GPS
        // If voltage is low, stop looking for GNSS and go to sleep
        get_vbat_smooth();
        if (vbat < VBAT_LOW) {
          break;
        }

#ifndef NoLED
        // 'Flash' the LED
        if ((millis() / 1000) % 2 == 1) {
          LED_dim_blue();
        }
        else {
          LED_blue();
        }
#endif

      }

      Serial.println(charsSeen ? fixFound ? F("A GPS fix was found!") : F("No GPS fix was found.") : F("Wiring error: No GPS data seen."));
      Serial.print("Latitude (degrees): "); Serial.println(latitude, 6);
      Serial.print("Longitude (degrees): "); Serial.println(longitude, 6);
      Serial.print("Altitude (m): "); Serial.println(altitude / 100); // Convert altitude from cm to m

      if (vbat < VBAT_LOW) {
        Serial.print("***!!! LOW VOLTAGE (read_GPS) ");
        Serial.print(vbat,2);
        Serial.println("V !!!***");
        loop_step = zzz;
      }
      else if (!charsSeen) {
        Serial.println("***!!! No GPS data received !!!***");
        loop_step = zzz;
      }
      else {
        loop_step = read_pressure;
      }
      
      break;

    case read_pressure:
      // Start the MPL3115A2 (does Wire.begin())
      if (baro.begin()) {
        // Read pressure twice to avoid first erroneous value
        pascals = baro.getPressure();
        pascals = baro.getPressure();
        if (pascals > 110000) pascals = 0.0; // Correct wrap-around if pressure drops too low
        tempC = baro.getTemperature();
      }
      else {
        Serial.println("***!!! Error initialising MPL3115A2 !!!***");
        pascals = 0.0;
        tempC = 0.0;
      }

      Serial.print("Pressure (Pascals): "); Serial.println(pascals,0);
      Serial.print("Temperature (C): "); Serial.println(tempC,1);

       // Power down the GPS and MPL3115A2
      Serial.println("Powering down the GPS and MPL3115A2...");
      digitalWrite(GPS_EN, GPS_OFF); // Disable the GPS and MPL3115A2

      loop_step = start_LTC3225;

      break;

    case start_LTC3225:

#ifndef NoLED
      LED_cyan(); // Set LED to Cyan
#endif

      // Power up the LTC3225EDDB super capacitor charger
      Serial.println("Powering up the LTC3225EDDB");
      Serial.println("Waiting for PGOOD to go HIGH...");
      digitalWrite(LTC3225shutdown, HIGH); // Enable the LTC3225EDDB supercapacitor charger
      delay(1000); // Let PGOOD stabilise
      init_vbat(); // init_vbat to make sure the current true smoothed voltage is used now that the LTC3225 is active
      
      // Allow 10 mins for LTC3225 to achieve PGOOD
      PGOOD = digitalRead(LTC3225PGOOD);
      for (tnow = millis(); !PGOOD && ((millis() - tnow) < 10UL * 60UL * 1000UL);)
      {
#ifndef NoLED
        // 'Flash' the LED
        if ((millis() / 1000) % 2 == 1) {
          LED_dim_cyan();
        }
        else {
          LED_cyan();
        }
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

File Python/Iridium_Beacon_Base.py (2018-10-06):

# -*- coding: cp1252 -*-

## Multi Iridium Beacon Base

## Written by Paul Clark: Dec 2017 - October 2018.

## This project is distributed under a Creative Commons Attribution + Share-alike (BY-SA) licence.
## Please refer to section 5 of the licence for the “Disclaimer of Warranties and Limitation of Liability”.

## Talks to an Iridium_9603N_Beacon_V5_Base via Serial over USB.
## Displays beacon and base locations using the Google Static Maps API:
## https://developers.google.com/maps/documentation/static-maps/intro
## You will need a Key to access the API. You can create one by following this link:
## https://developers.google.com/maps/documentation/static-maps/get-api-key
## Copy and paste it into a file called Google_Static_Maps_API_Key.txt

## Each beacon sends a data packet to the base via Iridium, forwarded by Rock7's RockBLOCK network.
## The serial number of the destination base can be set using the "Beacon Messaging" option (see below).

## Every 'update' seconds the GUI talks to the base beacon and:
## requests its GNSS data including time, position and altitude;
## starts an IridiumSBD session and downloads a packet from the mobile terminated queue
## (if any are present).

## The GUI and base provide access to the RockBLOCK FLUSH_MT function, so an excess of
## unread Mobile Terminated messages can be discarded if required
## (note that you are still charged from these messages!).

## The software logs all received packets to CSV log files. Each beacon gets its own log file.

## The software makes extensive use of the Google Static Map API.
## The displayed map is automatically centered on a new beacon position.
## The center position can be changed by left-clicking in the image.
## A right-click will copy the click location (lat,lon) to the clipboard.
## The zoom level is set automatically when a new beacon is displayed to show both beacon and base.
## The zoom can be changed using the buttons.

## Each beacon's path is displayed as a coloured line on the map.
## The oldest waypoints may be deleted as the map URL is limited to 8192 characters.

## A pull-down menu lists the locations of all the beacons being tracked.
## Clicking on a menu entry will center the map on that location and will copy the location
## to the clipboard.

## A second pull-down menu shows the location of the base. Clicking it will center the map on that
## location and will copy that location to the clipboard.

## The "Beacon Messaging" pull-down menu lets you send an SBD message _to_ the chosen beacon to - for example -
## change its message interval. The message format is:
## RBxxxxxxx[INTERVAL=yyy]
## where: xxxxxxx is the 'RockBLOCK' serial number of the 9603N (seven digits;
## prefix with zeros as necessary); and yyy is the message interval (BEACON_INTERVAL) in _minutes_.
## To operate a cut-down unit attached to that beacon, send the message
## RBxxxxxxx[RELAY=1]
## To enable message forwarding from the beacon to the base, send the message
## RBxxxxxxx[RBDESTINATION=yyyyy]
## where yyyyy is the RockBLOCK serial number of the _Base_ Iridium 9603N.
## To disable message forwarding, send the message
## RBxxxxxxx[RBDESTINATION=0]
## For more details, see https://github.com/PaulZC/Iridium_9603_Beacon/blob/master/RockBLOCK.md

## The GUI uses 640x480 pixel map images. Higher resolution images are available if you have a
## premium plan with Google.

## Offline maps can be collected using Google_Static_Map_Tiler.py
## Base and beacon locations will be shown on the offline maps but not path information

import Tkinter as tk
import tkMessageBox
import tkSimpleDialog
import tkFont
import serial
import time
import urllib
from PIL import Image, ImageTk, ImageDraw
import math
import numpy as np
from sys import platform
from shutil import copyfile
import os

class BeaconBase(object):

   def __init__(self):
      ''' Init BeaconBase: read API key; open the serial port; set up the Tkinter window '''
      print 'Multi Iridium 9603N Beacon Base'
      print
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

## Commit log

2016-10-06 First Release
    [Iridium_9603_Antenna.brd, Iridium_9603_Antenna.sch, Iridium_9603_Beacon.brd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]
2016-12-03 Substantial update following completion and test of the first PCB
    [Iridium_9603_Antenna.brd, Iridium_9603_Antenna.sch, Iridium_9603_Beacon.brd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]
2017-03-18 Substantial update following UBSEDS22I test flight
    [Iridium_9603_Antenna.brd, Iridium_9603_Antenna.sch, Iridium_9603_Beacon.brd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]
2017-04-16 Updates for Version 3
    Major update:
    Beacon can be operated from solar power
    GPS (GNSS) data now provided by u-blox SAM-M8Q
    [Iridium_9603_Beacon.brd, Iridium_9603_Beacon.sch]
2017-04-17 Small bug fix: converting iterationCounter to a string
    [Iridium9603Beacon.ino]
2017-04-17 Added a paste mask for V3 PCB
    The paste mask fiducials are oversized by 111% so will be the correct
    size when the mask apertures are undersized by 10%
    [Iridium_9603_Beacon_V3_Paste_Mask_All.brd]
2017-04-17 Improved the ground plane under the SAM-M8Q
    [Iridium_9603_Beacon.brd]
2017-04-18 Final tweaks before sending V3 for manufacture
    [Iridium_9603_Beacon.brd]
2017-09-16 Substantial update for V3
    Substantial update to match V3 of the PCB: now includes u-blox SAM-M8Q
    GNSS and the option of solar power
    [Iridium_9603_Antenna.brd, Iridium_9603_Antenna.sch, Iridium_9603_Beacon.brd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]
2017-09-16 Tidying up...
    [Iridium_9603_Antenna.brd, Iridium_9603_Antenna.sch, Iridium_9603_Beacon.brd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]
2017-09-16 Updates to match V3 PCB
2017-09-16 Updating LEARN.md (work in progress)
    [Iridium_9603_Antenna.brd, Iridium_9603_Antenna.sch]
2017-09-17 Added cable lengths for inclined solar panels
2017-12-27 Updated supercapacitor charger current draw.
2017-12-27 Read pressure twice to avoid first erroneous value
    [Iridium9603NBeacon.ino]
2018-01-01 Added V4 - Work In Progress!
    [Iridium_9603_Beacon.brd, Iridium_9603_Beacon.sch]
2018-01-04 Tested on Raspberry Pi. Updated zoom look-up table.
2018-01-27 Minor updates
    [Iridium_9603_Beacon.brd]
2018-02-04 Added split pads for supercapacitor charge current
    [Iridium_9603_Beacon.brd, Iridium_9603_Beacon.sch]
2018-02-04 Minor tweaks
    [Iridium_9603_Beacon.brd, Iridium_9603_Beacon.sch]
2018-02-07 Initial update for V4 - still work in progress
    [Iridium_9603_Antenna.brd, Iridium_9603_Antenna.sch, Iridium_9603_Beacon.brd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]
2018-02-08 Updated the PCB images
2018-02-11 Included full details of RockBLOCK gateway messaging
    [Iridium_9603_Beacon.brd, Iridium_9603_Beacon.sch]
2018-02-18 Added an option to power down the base 9603N
2018-03-06 Updated the BOM
2018-03-30 Added Python extras
    Added extra Python utilities to stitch the .bin SBD attachments together
    and convert them into KML format for Google Earth
2018-05-18 Major update for V5
    [Iridium_9603_Beacon.brd, Iridium_9603_Beacon.sch, Iridium_9603_Beacon_V5_BOM.xls]
2018-05-19 Added the Gerber files
    [copper_bottom.gbr, copper_top.gbr, drills.xln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]
2018-05-27 Added support for relay pulses
    Added support for relay pulses (to trigger e.g. a cut-down unit)
2018-05-28 Updated the Base code
    Updated the Base code:
    The relay pins are initialised - but not used.
    The Enable_9603N pin is initialised and used.
2018-06-09 Remote configuration of RockBLOCK messaging
    Previously it was only possible to enable RockBLOCK Gateway message forwarding by editing the Arduino code. This can now be done by sending Mobile Terminated messages through RockBLOCK Operations.
2018-07-07 Updated Iridium_Beacon_Base.py
    Updated Iridium_Beacon_Base.py: improved the blocking during Iridium communication. Added support for RGB tri-colour LED.
2018-08-04 Important Bugfix!
    Corrected a bug where the code would ignore an RBDESTINATION of 0 (i.e. message forwarding could not be disabled once enabled)
    [Iridium9603NBeacon_V5.ino]
2018-09-24 Added support for the new radio board
2019-01-17 Corrected the zero width polygons
    Corrected the zero width polygons in the micro USB connector that were causing problems for OSH Park. Thanks go to Paul Loewen @ usask.ca
    [Iridium_9603_Beacon.brd, Iridium_9603_Beacon.sch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]
2019-01-26 Added the stl and scad files for the covers
    [Cover_With_Radio.scad, Cover_With_Radio.stl, Cover_With_USB.scad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]
2019-09-22 Corrected the Mapper indentation
    [Iridium_Beacon_Mapper_RockBLOCK.py]

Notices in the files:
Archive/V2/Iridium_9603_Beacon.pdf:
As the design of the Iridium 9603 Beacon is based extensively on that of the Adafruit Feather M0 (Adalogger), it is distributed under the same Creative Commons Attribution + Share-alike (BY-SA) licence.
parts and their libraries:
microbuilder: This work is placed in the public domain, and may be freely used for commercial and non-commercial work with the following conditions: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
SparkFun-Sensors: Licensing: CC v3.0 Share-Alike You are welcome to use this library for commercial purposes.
